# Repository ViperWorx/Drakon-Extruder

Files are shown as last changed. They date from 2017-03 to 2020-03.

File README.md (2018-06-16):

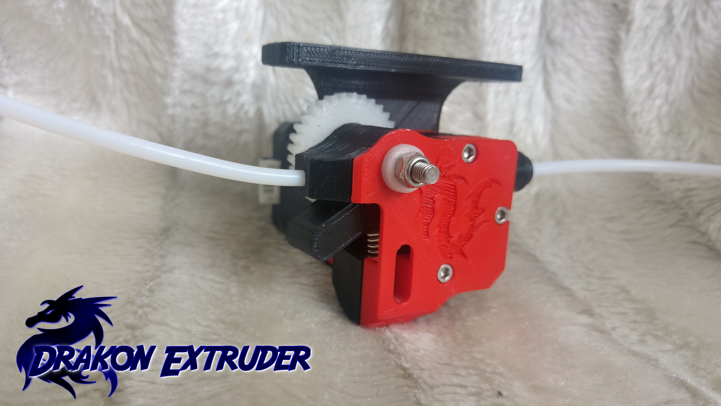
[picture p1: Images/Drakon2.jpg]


<h4>Reliability, Performance, Power</h4>

The Drakon has 3:1 gear reduction, fully FDM 3D Printed to keep costs down while performing as well as an extruder at 2-3 times the cost. The Gear ratio means that you’re able to use smaller, lighter motors while keeping the same pushing force as a standard non-geared extruder. For direct drive systems this means a lighter carriage, with less inertial mass, improving print quality. For Bowden systems running a standard sized motor means the Drakon becomes a power house of an extruder with all the power you’ll ever need to get your filament where it needs to go. In both Direct Drive and Bowden configurations you get the reliability and piece of mind to know that it’s not your extruder that’s going to fail.

<h4>Resolution</h4>

By increasing the gearing to 3:1, this triples the resolution, which can mitigate filament being extruded in pulses at slow speeds, which can result in a wavy surface finish, to give you a smooth surface finish. Note: This will not help other mechanical issues such as Z Wobble or Z Banding.

<h4>Materials</h4>

The Drakon has a fully supported filament path, which means it can print anything from flexibles, Carbonfills, metalfills and the hardest of filaments and beyond.

<h4>Universally easy to use</h4>

The Drakon strips down quickly with no need to remove the motor from it’s mounting, loosen the 3 bolts and just remove it from it’s mount. Remove the 8mm nut and bushing and that’s it, highly easy to maintain, should you need to take it apart for any reason. The Tensioner window allows you to easily see and set the tension quickly and precisely with no fuss. Easily mounted on a Direct Drive system as well as a Bowden. 

A full Bill of Materials can be found on the Wiki <a href=https://github.com/AxMod3DPrint/Drakon-Extruder/wiki/Bill-of-Materials>here</a>.

Assembly instructions can be found at <a href="https://youtu.be/jO8r4zXFYHI">https://youtu.be/jO8r4zXFYHI</a>

<hr />
<table border="0px">
<th align="left">
&copy; AxMod 3D Print 2017.
</th>
<tr>
<td>
This documentation describes Open Hardware and is licensed under the CERN OHL v. 1.2.
</td>
</tr>
<tr>
<td>
You may redistribute and modify this documentation under the terms of the
CERN OHL v.1.2. (http://ohwr.org/cernohl). This documentation is distributed
WITHOUT ANY EXPRESS OR IMPLIED WARRANTY, INCLUDING OF
MERCHANTABILITY, SATISFACTORY QUALITY AND FITNESS FOR A
PARTICULAR PURPOSE. Please see the CERN OHL v.1.2 for applicable
conditions
</td>
</tr>
</table>

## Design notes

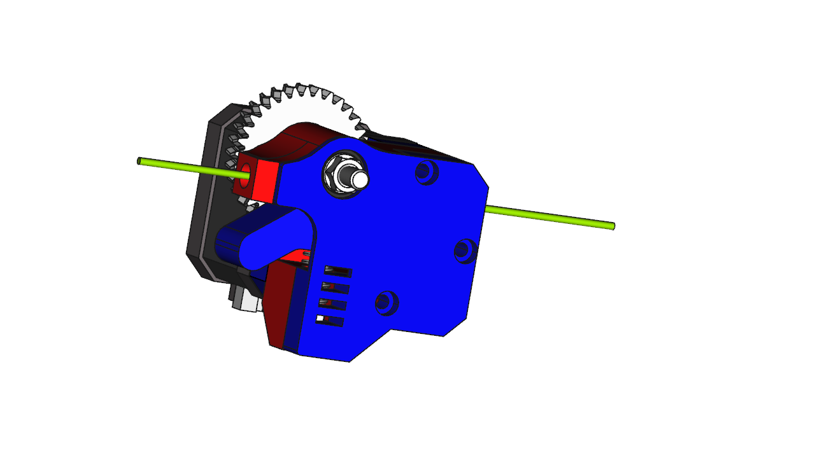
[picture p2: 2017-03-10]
Images/Extruder2.png

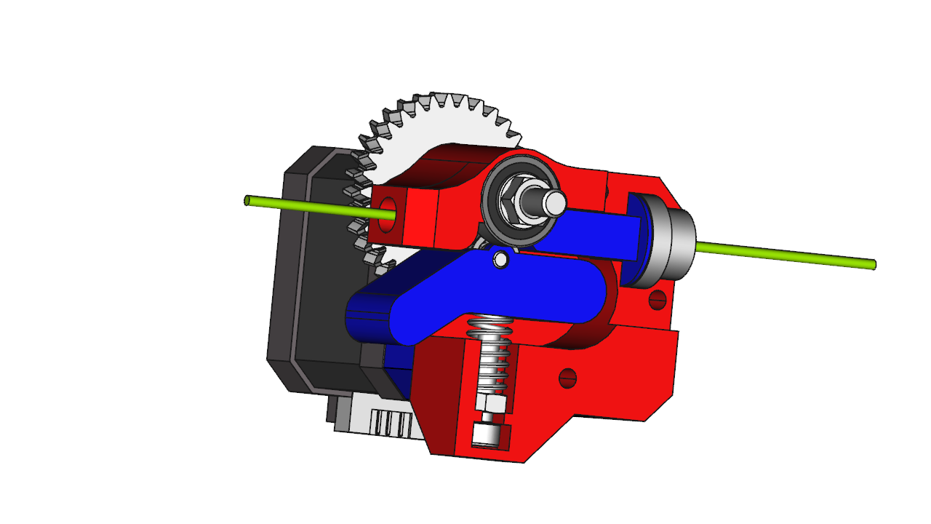
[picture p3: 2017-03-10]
Images/Extruder1.png

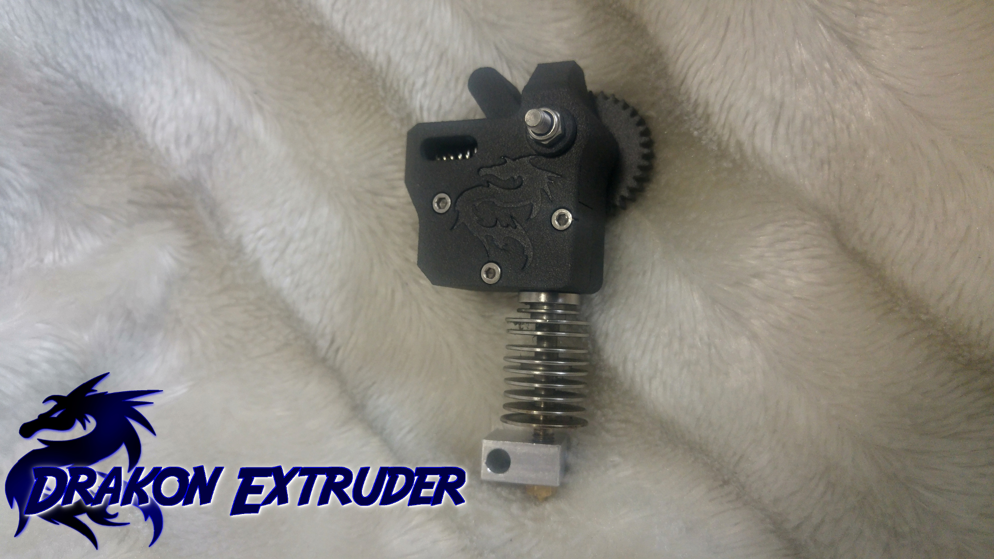
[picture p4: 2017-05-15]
Images/Drakon_SLS.jpg

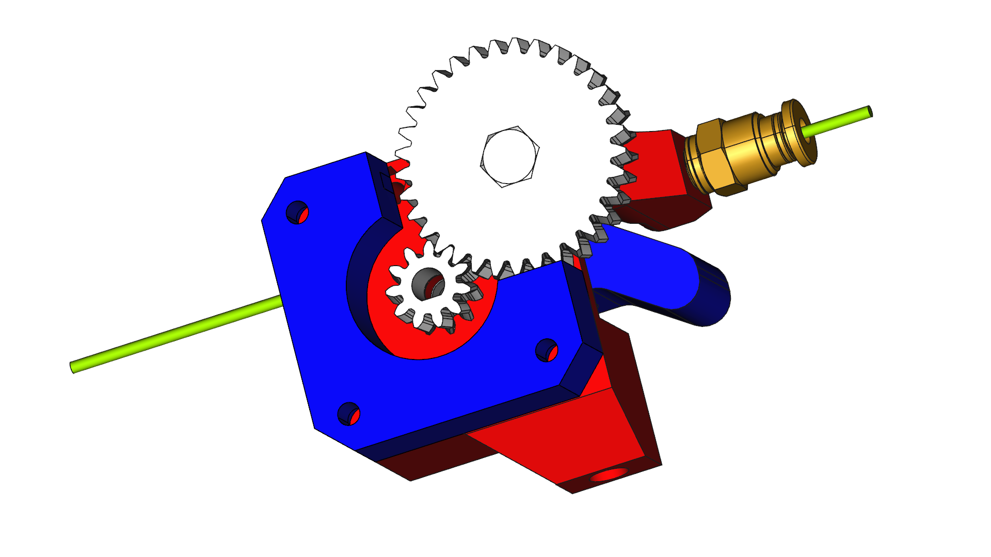
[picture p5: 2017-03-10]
Images/Extruder5.png

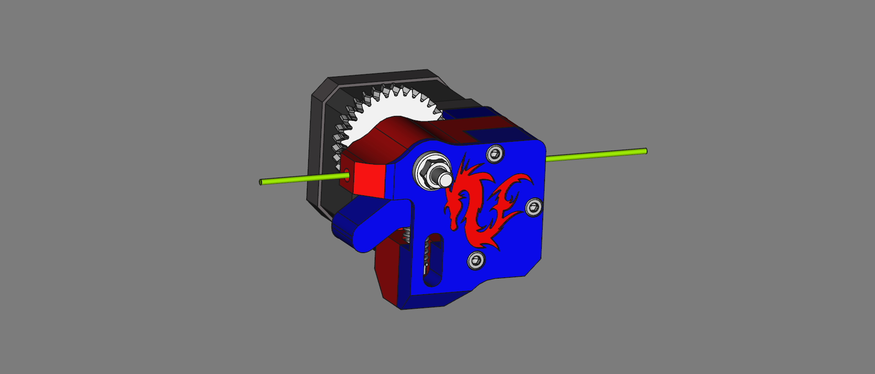
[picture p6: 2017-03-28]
Images/Extruder6.png

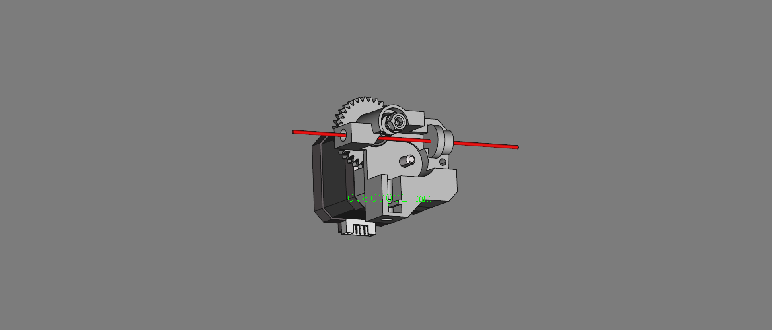
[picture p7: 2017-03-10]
Images/Extruder.png

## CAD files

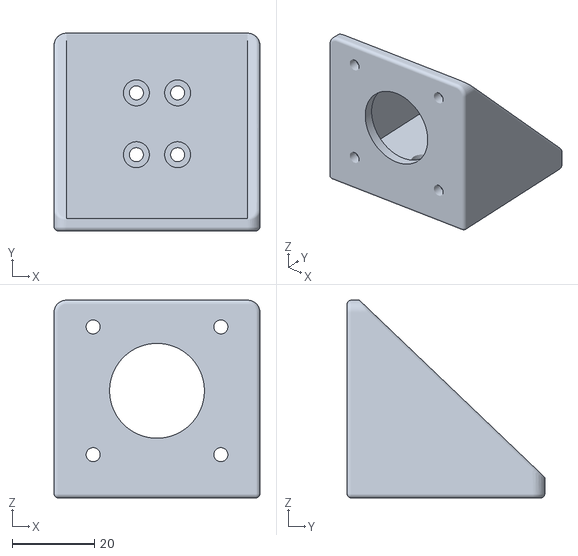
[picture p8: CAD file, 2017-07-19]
Extruder Mounts/Drakon_Direct_Drive_Mount_MakerBeam.stl
50.0 x 48.0 x 48.0

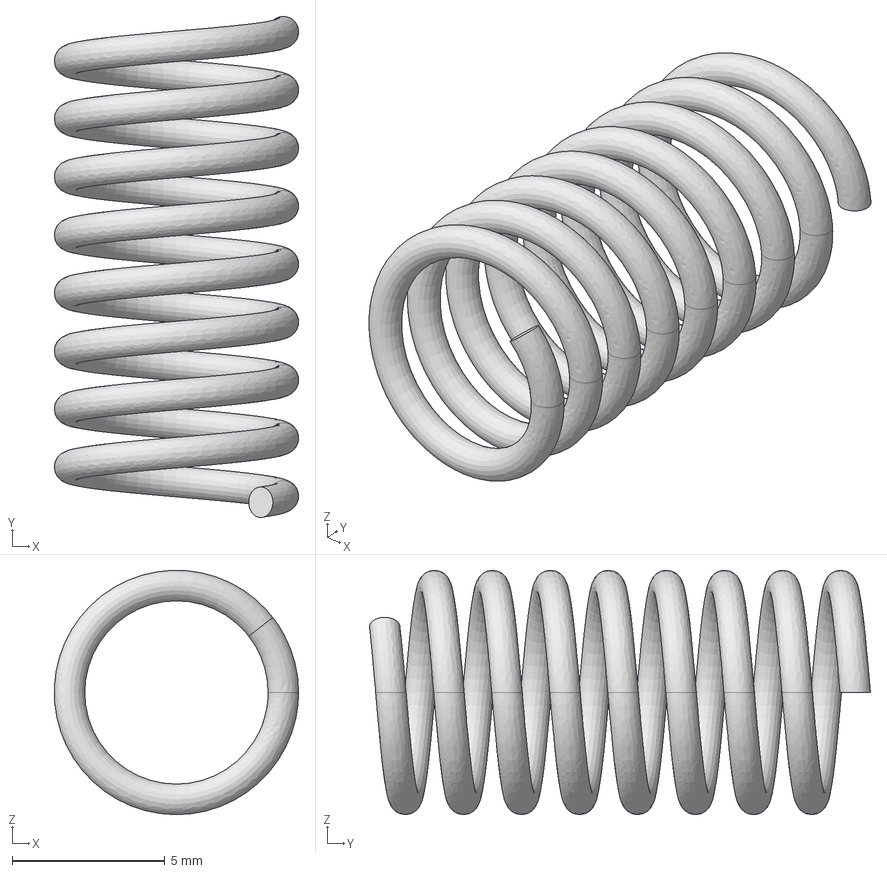
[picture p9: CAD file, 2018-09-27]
FreeCAD/STEP/Drakon_Spring.step
8.00 x 16.4 x 8.00 mm

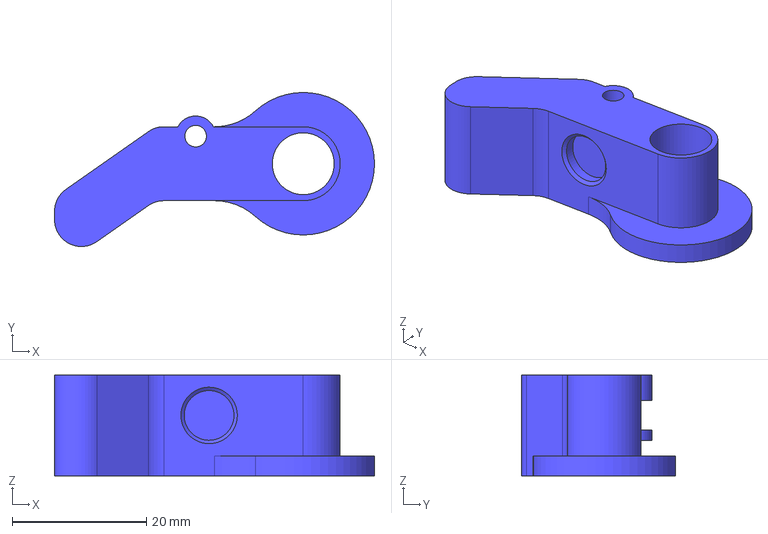
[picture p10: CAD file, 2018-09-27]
FreeCAD/STEP/Printed Parts/Drakon_1.75_Idler.step
47.6 x 22.9 x 15.0 mm

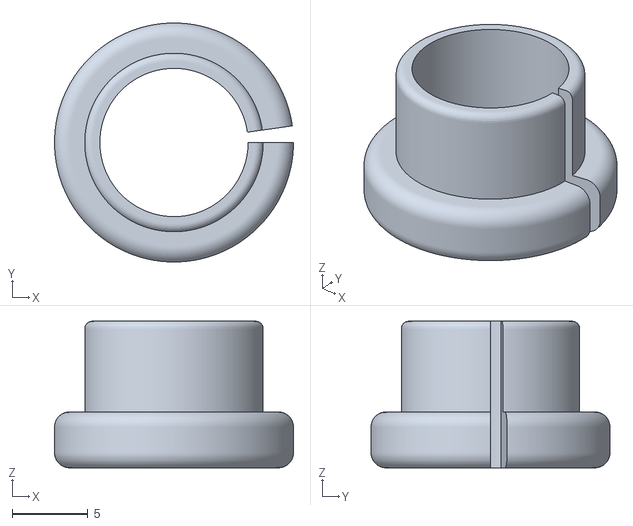
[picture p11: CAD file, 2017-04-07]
Groove Mount Adaptors/Drakon_Groove Mount Adaptor_E3D_Threaded_Bowden_Coupling.stl
15.8 x 15.8 x 9.70

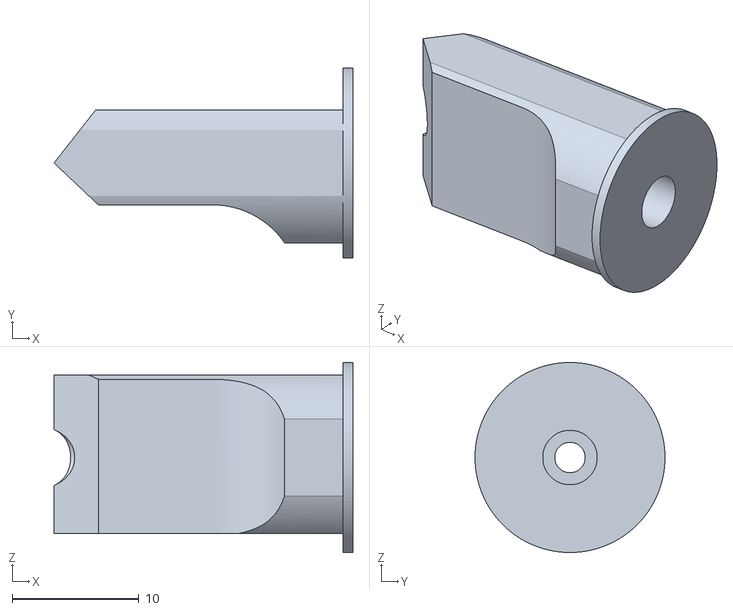
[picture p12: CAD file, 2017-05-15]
SLS Printable files/Drakon_Filament_Guide_SLS.stl
23.6 x 15.0 x 15.0

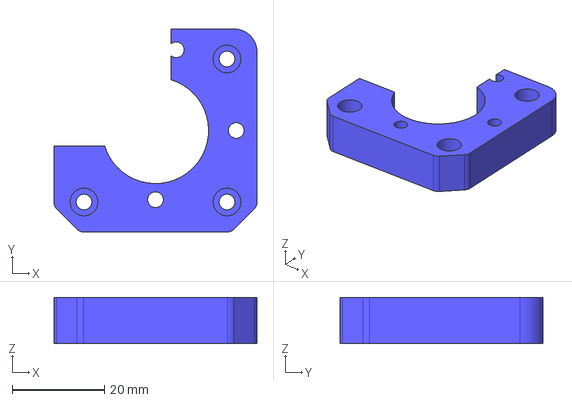
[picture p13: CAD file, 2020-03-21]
STEP/Drakon_Base.stp
44.0 x 44.0 x 10.0 mm

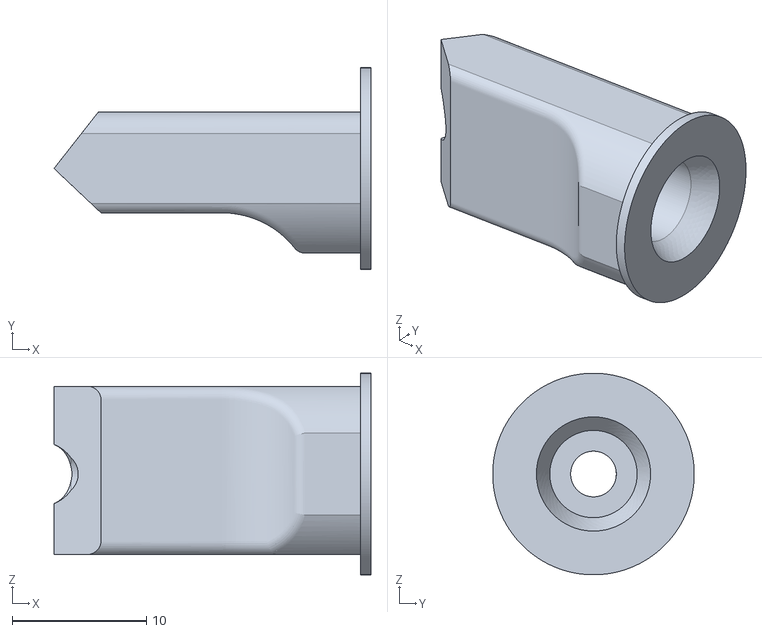
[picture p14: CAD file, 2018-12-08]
Untested_Drakon_Filament_Guide_3mm.stl
23.6 x 15.0 x 15.0

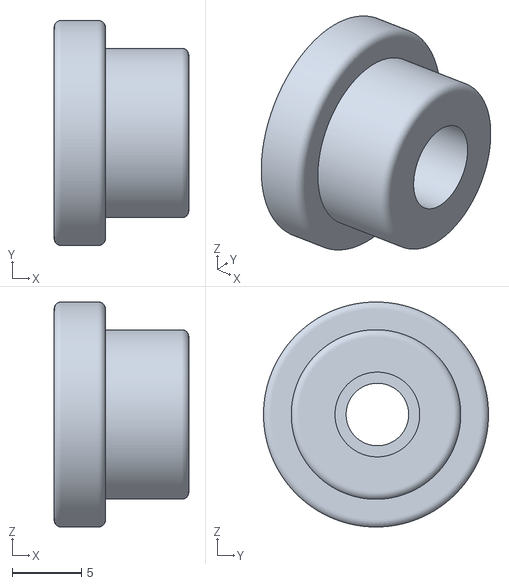
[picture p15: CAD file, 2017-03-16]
Groove Mount Adaptors/Drakon_Groove_Mount_Adaptor_PC4-M6.stl
9.70 x 16.2 x 16.2

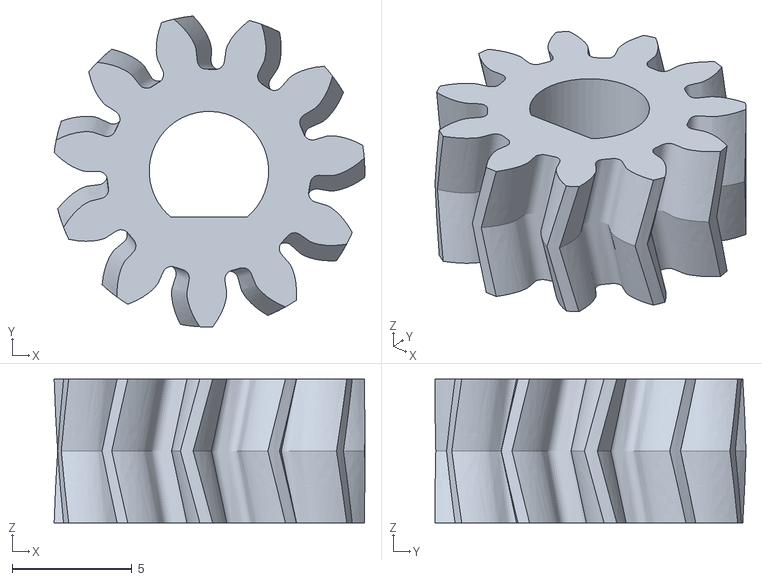
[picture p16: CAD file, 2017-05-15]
SLS Printable files/Drakon_Small_Gear_SLS.stl
13.0 x 13.0 x 6.00

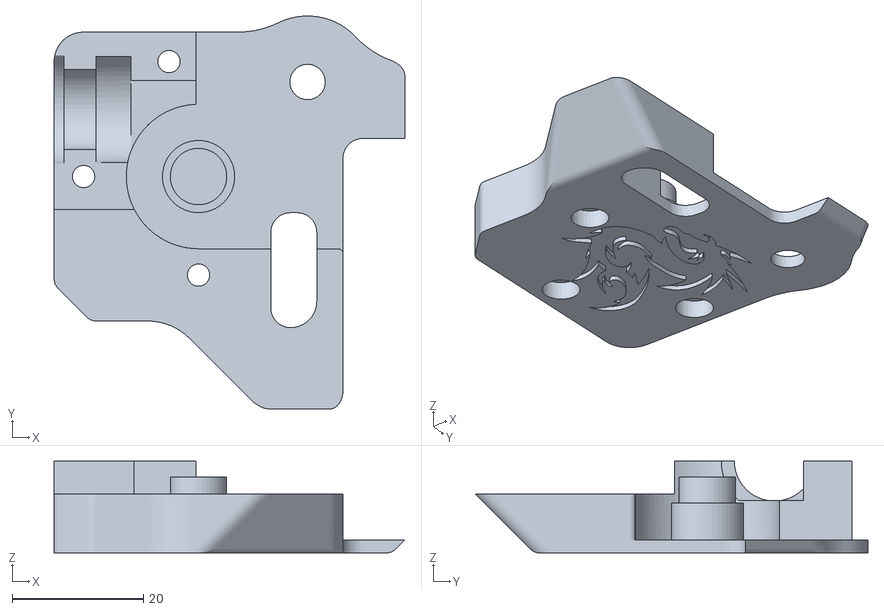
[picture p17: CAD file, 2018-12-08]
Drakon_Cover.stl
53.4 x 59.8 x 14.0

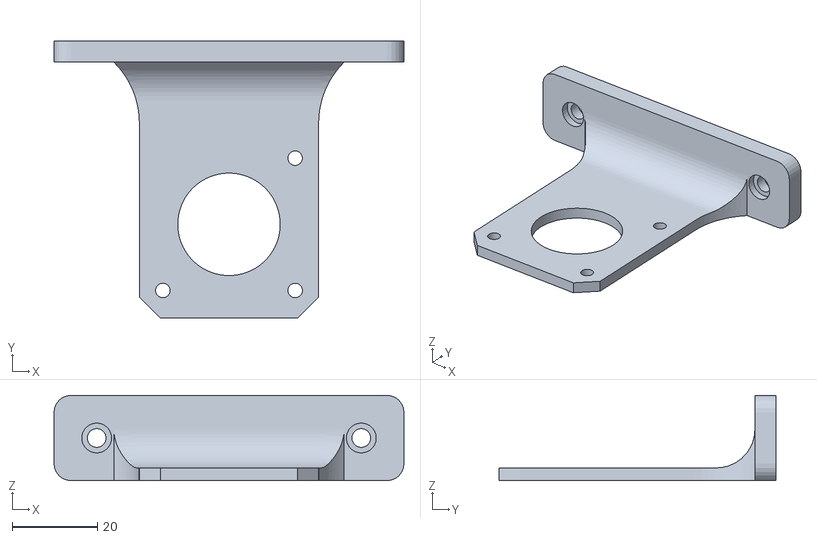
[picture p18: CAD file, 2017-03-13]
Extruder Mounts/Drakon_Frame_Mount.stl
82.0 x 65.0 x 20.0

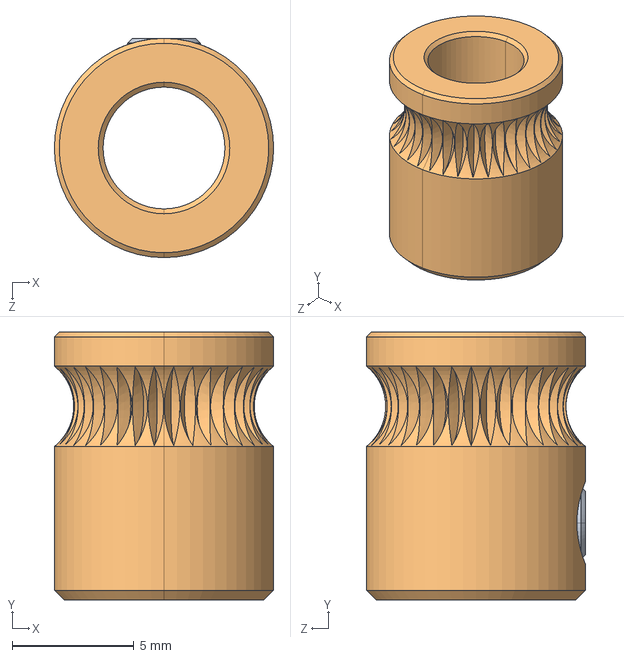
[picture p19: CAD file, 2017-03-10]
FreeCAD/STEP/MK8.STEP
9.00 x 11.0 x 9.00 mm

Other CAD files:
FreeCAD/Drakon_Direct_Drive_Mount_MakerBeam.fcstd
Drakon_Filament_Guide_1.75mm.stl
Extruder Mounts/Drakon_Direct_Drive_Mount.stl
FreeCAD/STEP/Printed Parts/Drakon_Filament_Guide.step
STEP/Drakon_1.75_Filament_Guide.stp
FreeCAD/STEP/Printed Parts/Drakon_Small_Gear.step
Drakon_Base.stl
Drakon_Body_1.75mm.stl
Drakon_Drive_Gear Spindle_Bushingx2.stl
Drakon_Idler.stl
Drakon_Large_Gear.stl
Drakon_Small_Gear.stl
FreeCAD/Dragon-Logo.fcstd
FreeCAD/Drakon_ Thumb_Screw.fcstd
FreeCAD/Drakon_Direct_Drive_Mount.fcstd
FreeCAD/Drakon_Frame_Mount.fcstd
FreeCAD/Drakon_Main_Bolt.fcstd
FreeCAD/Plastic_Through_Coupler_adaptor.fcstd
FreeCAD/STEP/623.STEP
FreeCAD/STEP/625ZZ.stp
FreeCAD/STEP/M5x40_Hex_Bolt.step
FreeCAD/STEP/PC4-M6_.stp
FreeCAD/STEP/PM Wantai 609 Nema 17.stp
FreeCAD/STEP/Printed Parts/Drakon_1.75_Body.step
FreeCAD/STEP/Printed Parts/Drakon_Base.step
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

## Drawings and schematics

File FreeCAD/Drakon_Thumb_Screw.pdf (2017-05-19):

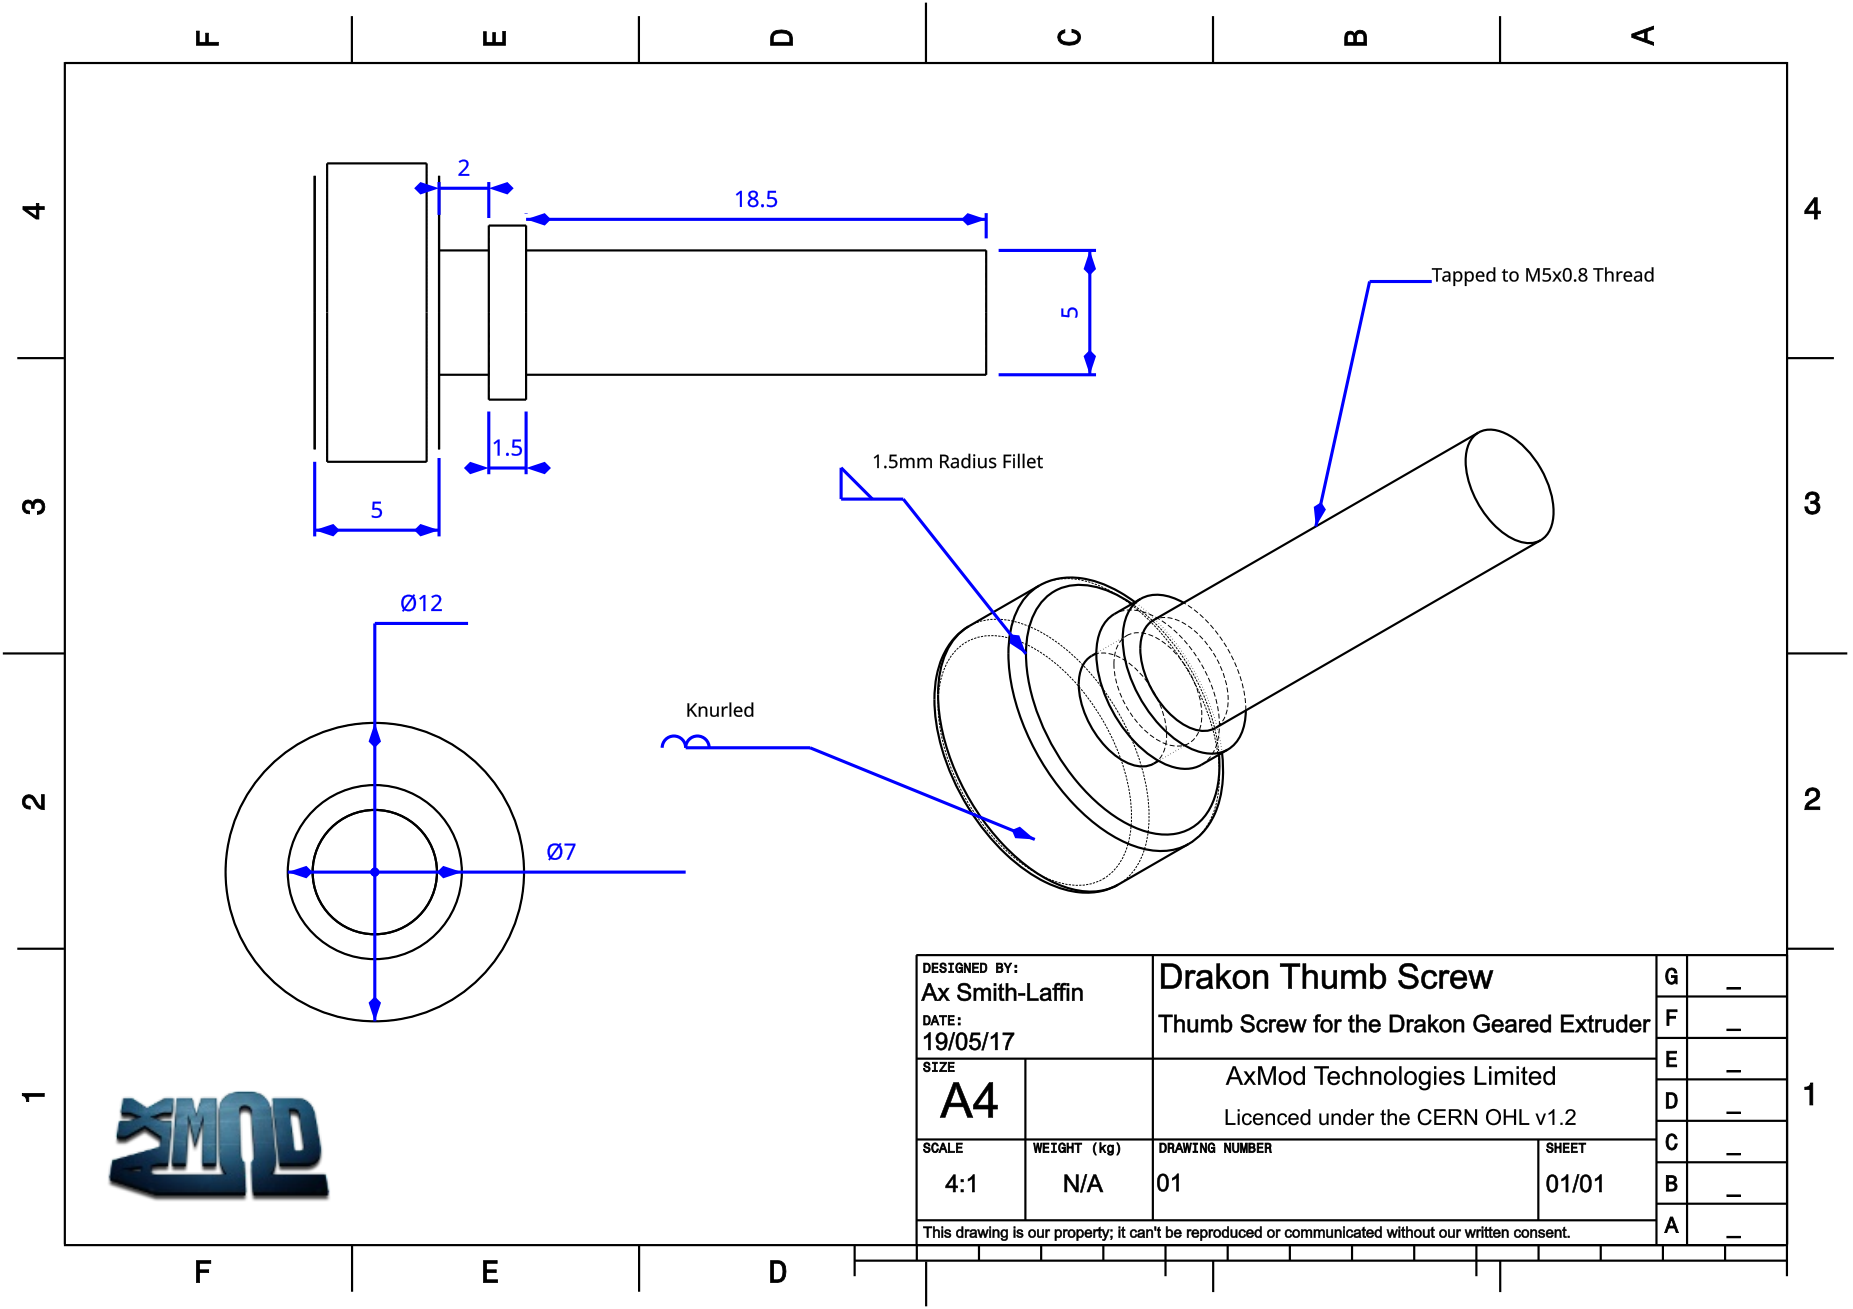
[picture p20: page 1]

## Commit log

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2017-03-11 Correct STL Orientation
    [Drakon_Base.stl, Drakon_Body.stl, Drakon_Cover.stl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]
2017-03-11 Correct bolt head size on large gear
    [Drakon_Large_Gear.stl]
2017-03-11 Reduce flat in hole to 2.5mm from 3mm
    [Drakon_Small_Gear.stl]
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2017-03-11 Add 0.2mm tolerance to Small gear centre hole
    [Drakon_Small_Gear.stl]
2017-03-11 Extend bolt holes and add nut traps
    Herp derp forgot that this needs mounting to the motor
    [Drakon_Base.stl]
2017-03-11 Correct filament path
    moved down 2mm and in 1mm
    [Drakon_Body.stl, Drakon_Cover.stl, Drakon_Filament_Guide.stl]
2017-03-11 Move Spring pocket up 0.5mm - correct position of bearing
    Idler bearing position corrected relative to new filament path bearing pocket has been enlarged to allow free movement
    [Drakon_Idler.stl]
2017-03-11 Add Cover with no logo
    [Drakon_Cover_No_Logo.stl]
2017-03-11 Add Body with internal spindle for idler arm
    will allow for not using the MR95ZZs
    [Drakon_Body_Idler_Arm_Spindle.stl]
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2017-03-12 Enlarge Groove Mount - Correct Filament Guide seat
    [Drakon_Body.stl, Drakon_Body_Idler_Arm_Spindle.stl]
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2017-03-12 Correct Orientation for printing
    [Drakon_Idler.stl]
2017-03-12 Moveve filament path 0.5mm toward centre
    [Drakon_Body.stl, Drakon_Body_Idler_Arm_Spindle.stl, Drakon_Cover.stl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]
2017-03-12 Move filament path 0.5mm toward centre
    [Drakon_Body.stl, Drakon_Body_Idler_Arm_Spindle.stl, Drakon_Cover.stl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]
2017-03-13 Reduce large gear hole in cover to support body enlarge tension holes
    [Drakon_Cover.stl, Drakon_Cover_No_Logo.stl]
2017-03-13 Add Bowden Mount for Extrusion based printers
    [Drakon_Frame_Mount.fcstd, Drakon_Frame_Mount.stl]
2017-03-14 Add small tolerance to cover to allow for better fit
    [Drakon_Cover.stl, Drakon_Cover_No_Logo.stl]
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2017-03-15 Correct printing orientation
    [Drakon_Large_Gear.stl]
2017-03-15 Add base to idler arm
    [Drakon_Idler.stl]
2017-03-15 Add Bushings, remove M5 Washers
    [Drakon_Drive_Gear Spindle_Bushingx2.stl]
2017-03-15 remove 0.1mm from bottom bearing seat depth - deepen tension spring seat
    [Drakon_Body.stl, Drakon_Body_Idler_Arm_Spindle.stl, Drakon_Body_MR95ZZ.stl]
2017-03-16 Add Groove Mount Adaptor for PC4-M6 & PC4-10
    [Drakon_Groove_Mount_Adaptor_PC4-10.stl, Drakon_Groove_Mount_Adaptor_PC4-M6.stl]
2017-03-16 Add Filament guide for direct drive - pocket for collet added
    [Drakon_Filament_Guide_Direct_Drive.stl]
2017-03-28 Remove MR95ZZ option - not needed
    [Drakon_Body_Idler_Arm_Spindle.stl, Drakon_Body_MR95ZZ.stl]
2017-03-28 Reduce Tolerances, remove need for PC4M6 on input
    Groove Mount reduced by 0.1mm
    Tension Spring seat reduced by 0.2mm
    Remove PC4M6 seat in favour of directly inserting tube into body
    [Drakon_Body.stl]
2017-03-28 Reduce tolerances, change tension guide, change logo
    Tolerances changed to match commit c14037ffef90ed8a7c9795b4c055323976e392a9
    Logo has had eye part removed as it is really too small to print
    Change tension guide to Window for easier viewing of tension
    [Drakon_Cover.stl, Drakon_Cover_No_Logo.stl]
2017-03-28 Change to All in one Filament guide
    No point in having 2 guides when the Direct drive will work for both
    [Drakon_Filament_Guide.stl, Drakon_Filament_Guide_Direct_Drive.stl]
2017-03-28 Add SLS printable versions of gears and bushings
    [Drakon_Drive_Gear Spindle_Bushingx2_SLS.stl, Drakon_Large_Gear_SLS.stl, Drakon_Small_Gear_SLS.stl]
2017-03-28 CAD updates to recent changes
    [Dragon-Logo.fcstd]
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2017-03-28 Move SLS STLs to their own folder
    [Drakon_Drive_Gear Spindle_Bushingx2_SLS.stl, Drakon_Large_Gear_SLS.stl, Drakon_Small_Gear_SLS.stl]
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2017-03-28 Make Manifold, correct oreintation
    Raw STLs for cover are not manifold - fixed
    Correct oreintation for printing
    [Drakon_Cover.stl, Drakon_Cover_No_Logo.stl]
2017-03-28 Easier inserting of Filament
    Widened mouth of Filament guide to make filament easier to insert
    [Drakon_Filament_Guide.stl]
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2017-04-07 Move groove mount adaptors to own folder - add new adaptor
    New adaptor for http://e3d-online.com/E3D-v6/Spares/Threaded-Bowden-Coupling-1.75mm-Filament
    [Drakon_Groove Mount Adaptor_Through_Coupler.stl, Drakon_Groove_Mount_Adaptor_PC4-10.stl, Drakon_Groove_Mount_Adaptor_PC4-M6.stl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]
2017-04-07 Correct orientation
    [Drakon_Cover.stl]
2017-04-07 Change name of file for clarity
    [Drakon_Groove Mount Adaptor_E3D_Threaded_Bowden_Coupling.stl]
2017-04-09 Add small 0.6mm fillets
    added to Tensioner spring channel and underside of body motor spindle hole
    [Drakon_Body.stl]
2017-04-09 Add 0.6mm fillet, reduce idler bearing seat size
    0.6mm fillet added to underside of spindle hole
    idler bearing seat reduced to 4.4mm in height - packing washers no longer needed
    [Drakon_Idler.stl]
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2017-04-09 Reduce Bolt head seat by 1.5mm
    [Drakon_Large_Gear.stl]
2017-04-09 Add Files for SLS 3D Printing
    [Drakon_Base_SLS.stl, Drakon_Body_SLS.stl, Drakon_Cover_SLS.stl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]
2017-04-09 Move Bolt hole
    Bolt hole on Groove mount moved in 0.5mm to prevent STL becoming non-manifold
    [Drakon_Base.stl, Drakon_Body.stl, Drakon_Cover.stl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]
2017-04-09 New Filament Guide design
    [Drakon_Filament_Guide.stl]
2017-04-09 Drop idler bearing by 1mm
    Was not properly aligned with filament path
    [Drakon_Idler.stl]
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2017-04-09 SLS Idler
    changed to reflect commit f9bee95f08c6e41a0b883e2b43869f88878935cb
    [Drakon_Idler_Arm_SLS.stl]
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2017-04-13 Remove need for support on Filament guide
    [Drakon_Filament_Guide.stl]
2017-04-15 Revert drop idler bearing by 1mm
    [Drakon_Idler.stl]
2017-04-21 Filament guide - Remove hotend collet seat - not needed
    Collet seat not needed - collet is not needed when using the Drakon in DD
    [Drakon_Filament_Guide.stl]
2017-05-12 Increase Tolerance, raise idler bearing
    Idler bearing raised 1mm
    Increase bearing seat tolerance
    drop spring seat 1mm
    [Drakon_Idler_Arm_SLS.stl]
2017-05-12 Move mount holes, increase tensioner seat thickness, tolerances
    Bolt head of tensioner bolt seat outer thickness increased to 2.5mm, whole tensioner seat dropped 1mm and increase seat length by 2mm
    Move mount holes to stop gaps in print - increase hole tolerance by 0.05mm radius
    Cover - added meat to main spindle hole
    [Drakon_Base_SLS.stl, Drakon_Body_SLS.stl, Drakon_Cover_SLS.stl]
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2017-05-15 Recess Bearing retaining bolt further
    Bolt was clashing with bearing causing it not to grip the filament
    [Drakon_Idler_Arm_SLS.stl]
2017-05-15 Drop bottom drive bolt bearing by 0.5mm
    adding 0.5mm clearance to stop the large gear rubbing against the body
    [Drakon_Body_SLS.stl]
2017-05-15 Increase tolerance of motor shaft hole
    Hole is way to tight, was at 4.9mm diameter, increased to 4.98mm
    [Drakon_Small_Gear_SLS.stl]
2017-05-15 Remove Collet seat, increase inner diameter
    Collet seat not needed, collet on hot end does not need to be installed to use the Drakon. Also removes thin wall which does not print.
    Increased inner Diameter of Tube seat from 2.1mm radius to 2.15mm radius. Tube is slightly tight on insertion,
    [Drakon_Filament_Guide_SLS.stl]
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2017-05-15 Drop Spring seat by 1mm, increase retaining bolt seat pocket
    Increased retaining bolt seat to 5.3mm to add clearance for bottom drive bolt bearing
    Drop spring seat by 1mm so it is pushing directly behind the idler bearing
    [Drakon_Idler.stl]
2017-05-15 Add missed chamfer, drop tensioner spring seat by 1mm
    Tensioner spring seat dropped by 1mm to allow spring to push directly behind the idler bearing
    Chamfered idler spindle to allow for easy seating of idler arm.
    [Drakon_Body.stl]
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2017-05-16 Add Generic Direct Drive mount for the Drakon
    [Drakon_Direct_Drive_Mount.fcstd, Drakon_Direct_Drive_Mount.stl]
2017-05-17 Small edit
    Forgot to commit, so have no clue what changed - see comparison on GitHub
    [Drakon_Idler.stl]
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2017-06-06 Add 3mm FDM printable version
    Rename files for clarity and add 3mm filament versions of body and filament guide.
    Rename 1.75mm files
    [Drakon_Body_1.75mm.stl, Drakon_Body_3mm.stl, Drakon_Filament_Guide_1.75mm.stl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]
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2017-06-06 Add Main Bolt CAD
    [Drakon_Main_Bolt.fcstd]
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2017-07-19 Export STL and Move mounts into their own folder
    [Drakon_Direct_Drive_Mount.stl, Drakon_Direct_Drive_Mount_MakerBeam.stl, Drakon_Frame_Mount.stl]
2018-06-16 Add Clearance in Body to allow for long grub screws
    Longer grub screws on hobbed gears were slightly fouling the body and causing resistance. 0.75mm clearance added to prevent this
    [Drakon_Body_1.75mm.stl]
2018-08-28 Fix Large Gear Mesh
    File had self intersecting faces
    [Drakon_Large_Gear.stl]
2018-08-28 Fix Small Gear Mesh
    Mesh had intersecting faces
    [Drakon_Small_Gear.stl]
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2018-09-27 Several areas thickened, tensioner area pulled out
    Bearing seat outer area thickened to make it easier to print. Tensioner area moved to allow greater range of tension to allow better printing of flexibles and assembly
    [Drakon_Body_1.75mm.stl, Drakon_Cover.stl]
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2018-09-27 Round off / Thicken several areas to match main body
    [Drakon_Base.stl]
2018-09-27 Add Step of spring and M5 hex Bolt
    [Drakon_Spring.step, M5x40_Hex_Bolt.step]
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
